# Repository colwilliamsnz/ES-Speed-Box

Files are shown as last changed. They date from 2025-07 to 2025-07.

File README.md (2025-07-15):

# ES-Speed-Box for controlling Pro-Ject Turntables with 16VAC Synchronous Motors.

## Status:

Prototype.

## Introduction:

A speed controller to suit Pro-Ject Turntables with 16VAC synchronous motors (Expression 3, etc). A clone of sorts of the off the shelf line of Pro-ject "SpeedBox" devices that allows for 33RPM and 45RPM speed selection electronically instead of changing the belt/pulley beneath the turntable platter.

Speed selection is controlled in software using a DDS (direct digital synthesis) IC to generate a sinusoidal waveform of the appropriate frequency (~50Hz for 33RPM, ~67 for 45RPM). An I2C header allows for an optional external OLED screen to display speed selection. An 18VDC output provides power to a Pro-Ject Phonobox. The device can be WiFi enabled to allow the speed to be controlled remotely using MQTT auto-discovery via HomeAssistant.

Power to the circuit is controlled via an SSR (solid state relay) and is intended to be connected to a 12V amplifier trigger output. Thus the device has no phantom power draw and only powers the turntable when the amplifier trigger output is on.

## Project Goals:

1. Powered on when the amplifier is on/phono aux input is on.
2. Provide power to both the turntable but also an Phono Box II pre-amp.
3. I2C interface to allow connection of an OLED screen to display speed and amp volume (amp volume via Yamaha API).
4. Low profile design to fit in a small rack mountable case.

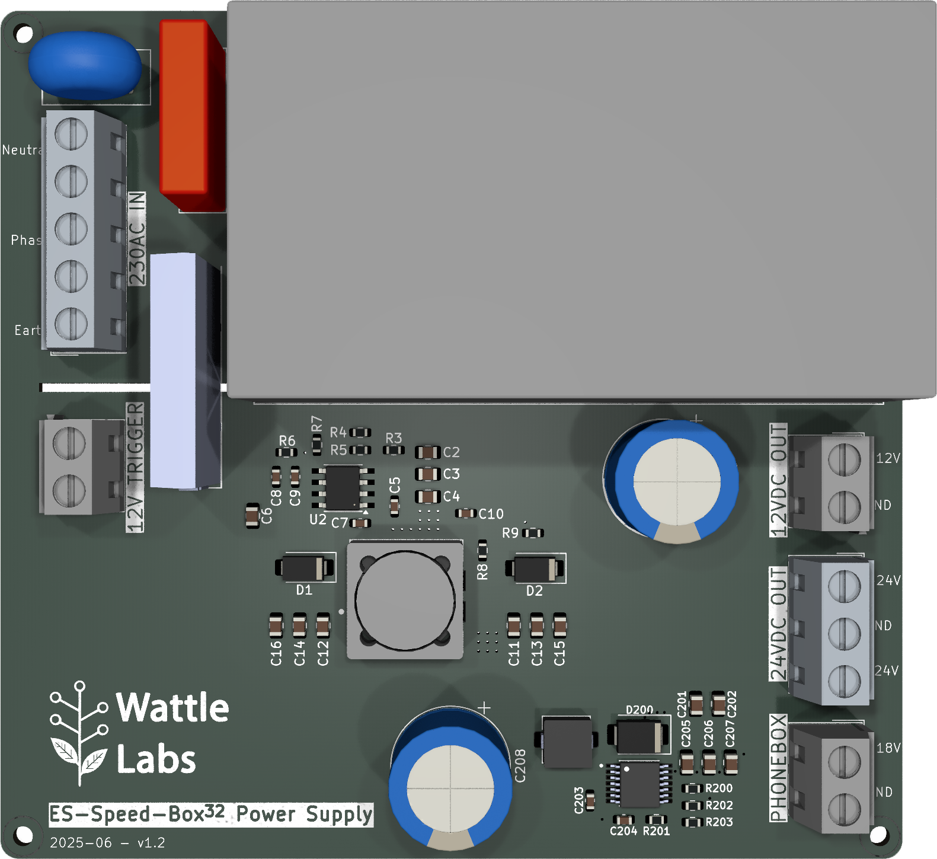
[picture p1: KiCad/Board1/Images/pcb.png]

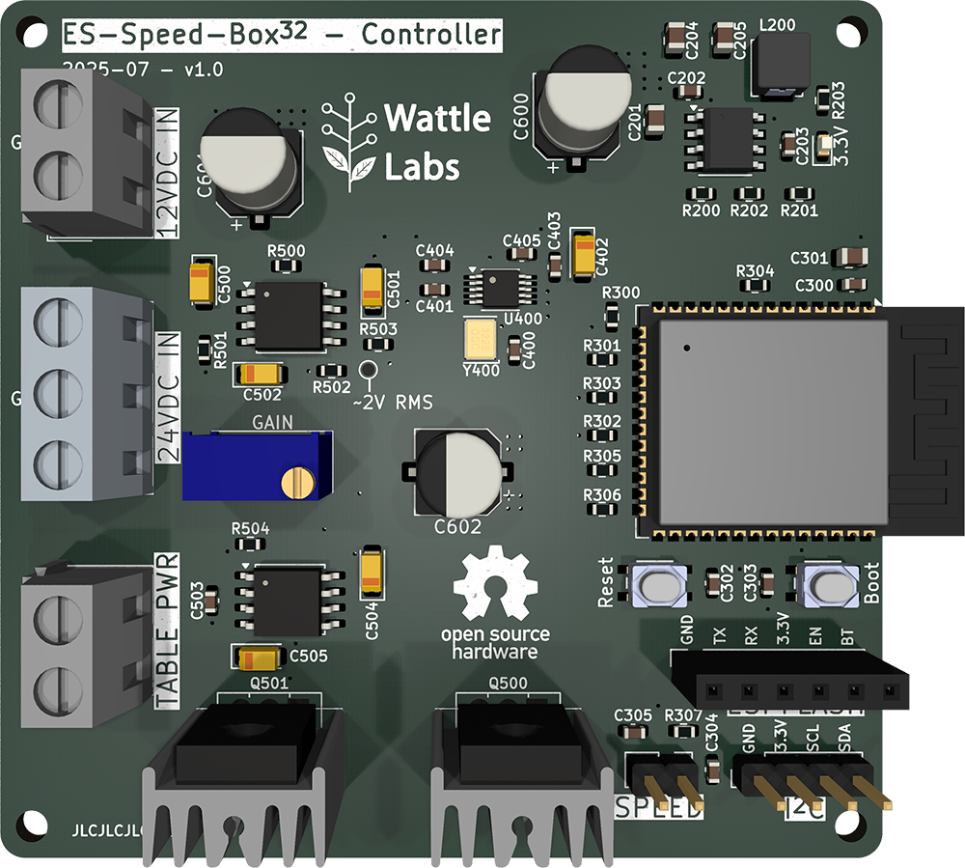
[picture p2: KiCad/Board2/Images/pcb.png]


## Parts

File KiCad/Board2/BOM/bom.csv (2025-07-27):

Reference | Value | Footprint | Qty | Digikey_PN
C402,C500 | 10u | Capacitor_Tantalum_SMD:CP_EIA-3216-18_Kemet-A | 2 | 399-8269-1-ND
C501,C502,C504,C505 | 1u | Capacitor_Tantalum_SMD:CP_EIA-3216-18_Kemet-A | 4 | 478-1651-1-ND
C600,C601,C602 | 47u | Capacitor_SMD:CP_Elec_6.3x7.7 | 3 | 493-2225-1-ND
L200 | 4.7uH | Wattle_Inductors:Bournes_SRP4020TA-4R7M | 1 | SRP4020TA-4R7MCT-ND
Q500 | BD139 | Package_TO_SOT_THT:TO-126-3_Vertical | 1 | 497-6656-5-ND
Q501 | BD140 | Package_TO_SOT_THT:TO-126-3_Vertical | 1 | 497-6657-5-ND
RV500 | 10k | Wattle_Trimpots:PV36W103C01B00 | 1 | 118-PV36W103C01B00-ND
SW300 | Reset | Wattle_Switches:PTS810 | 2 | CKN10878CT-ND
U200 | AP64352Q | Wattle_Regulators:AP64352QSP-13 | 1 | 31-AP64352QSP-13CT-ND
U300 | ESP32-S3-WROOM-1 | RF_Module:ESP32-S3-WROOM-1 | 1 | 1965-ESP32-S3-WROOM-1U-N8CT-ND
U400 | AD9833BRMZ | Package_SO:MSOP-10_3x3mm_P0.5mm | 1 | AD9833BRMZ
U500,U501 | OPA604AU/2K5 | Package_SO:SOIC-8_5.3x5.3mm_P1.27mm | 2 | 296-46167-1-ND
Y400 | 24Mhz | Oscillator:Oscillator_SMD_EuroQuartz_XO32-4Pin_3.2x2.5mm | 1 | 1908-O240-JO32-B-1V3-1-T1-LFCT-ND

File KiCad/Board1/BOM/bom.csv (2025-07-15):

Reference | Value | Footprint | Qty | Digikey_PN
C1 | 10n | Capacitor_THT:C_Rect_L18.0mm_W5.0mm_P15.00mm_FKS3_FKP3 | 1 | BFC233841103-ND
C2,C3,C4,C6,C11,C12,C13,C14,C15,C16 | 22u | Capacitor_SMD:C_0805_2012Metric | 10 | 445-14428-1-ND
C5,C7,C8 | 100n | Capacitor_SMD:C_0603_1608Metric | 3 | 587-3354-1-ND
C9 | 330p | Capacitor_SMD:C_0603_1608Metric | 1 | 399-C0603C331K5RACTUCT-ND
C10 | 470p | Capacitor_SMD:C_0603_1608Metric | 1 | 399-C0603C471F5GACTUCT-ND
C200,C208 | 1000u | Capacitor_THT:CP_Radial_D13.0mm_P5.00mm | 2
C201,C202 | 10u | Capacitor_SMD:C_0805_2012Metric | 2 | 490-10515-1-ND
C203 | 47n | Capacitor_SMD:C_0603_1608Metric | 1 | 490-5854-1-ND
C204 | 15n | Capacitor_SMD:C_0603_1608Metric | 1 | 311-1430-1-ND
C205,C206,C207 | 4.7 | Capacitor_SMD:C_0805_2012Metric | 3 | 490-10751-1-ND
D1,D2 | B360A | Diode_SMD:D_SMA | 2 | B360A-M3/61TGICT-ND
D200 | B360B-13-F | Diode_SMD:D_SMB | 1 | B360B-FDICT-ND
L1 | 2x33uH | Wattle_Inductors:Bournes_SRF1260-330M | 1 | SRF1260-330MCT-ND
L200 | 10uH | Wattle_Inductors:Bournes_SRP5030T-100M | 1 | SRP5030T-100MCT-ND
R1,R2 | 2M | Resistor_SMD:R_2010_5025Metric_Pad1.40x2.65mm_HandSolder | 2 | 2019-HV732HTTE2004FCT-ND
R3 | 280k | Resistor_SMD:R_0603_1608Metric | 1 | 311-280KHRCT-ND
R4 | 49.9k | Resistor_SMD:R_0603_1608Metric | 1 | 541-3989-1-ND
R5 | 412k | Resistor_SMD:R_0603_1608Metric | 1 | 311-412KHRCT-ND
R6 | 10k | Resistor_SMD:R_0603_1608Metric | 1 | A121523CT-ND
R7 | 2k | Resistor_SMD:R_0603_1608Metric | 1 | 541-3953-1-ND
R8 | 100 | Resistor_SMD:R_0603_1608Metric | 1 | 311-100HRCT-ND
R9 | 118k | Resistor_SMD:R_0603_1608Metric | 1 | 541-118KHCT-ND
R200 | 105k | Resistor_SMD:R_0603_1608Metric | 1 | 13-AC0603FR-07105KLCT-ND
R201 | 3.83k | Resistor_SMD:R_0603_1608Metric | 1 | 311-3.83KHRCT-ND
R202 | 221k | Resistor_SMD:R_0603_1608Metric | 1 | 311-221KHRCT-ND
R203 | 16.2k | Resistor_SMD:R_0603_1608Metric | 1 | 311-16.2KHRCT-ND
RV1 | 10D561 | Varistor:RV_Disc_D12mm_W6.1mm_P7.5mm | 1 | 118-MOV-10D561K-ND
S1 | AQG22212 | Wattle_Relays:AQG22212 | 1 | 255-3751-ND
U1 | IRM-30-12 | Wattle_Power:IRM-30-12 | 1 | 1866-3043-ND
U2 | TPS54340DDA | Package_SO:TI_SO-PowerPAD-8_ThermalVias | 1 | 296-35495-5-ND
U200 | TPS61175PWPR | Wattle_Regulators:TPS61175 | 1 | 296-24013-1-ND

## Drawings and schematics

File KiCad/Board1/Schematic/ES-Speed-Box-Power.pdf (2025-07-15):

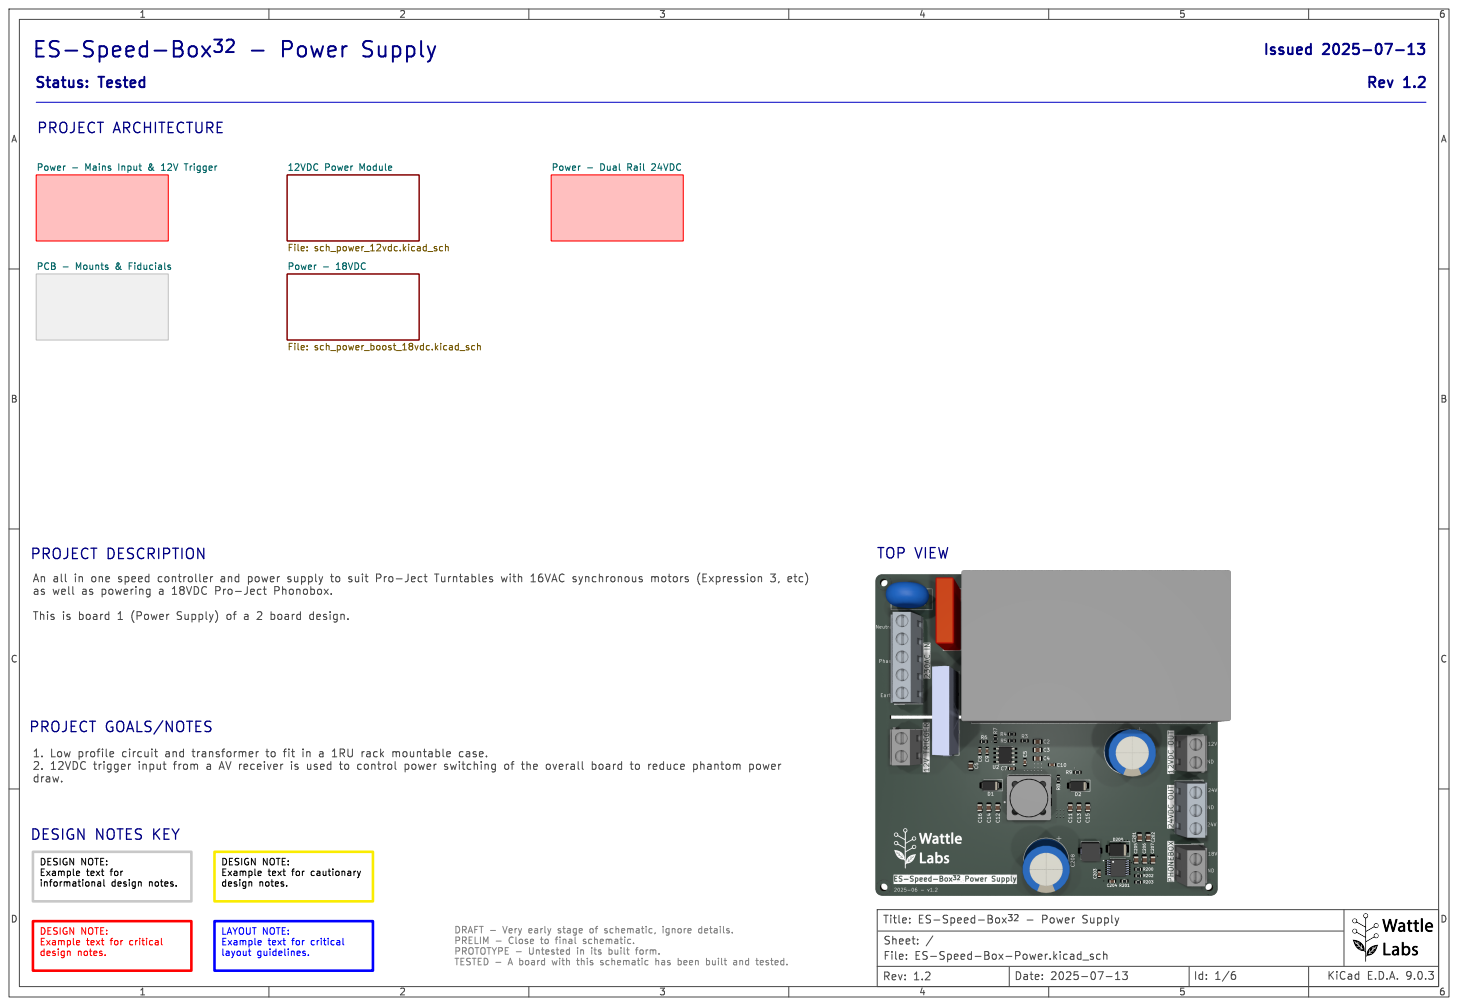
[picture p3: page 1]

DESIGN NOTE: Example text for critical design notes. DESIGN NOTE: Example text for

design notes. LAYOUT NOTE: Example text for critical

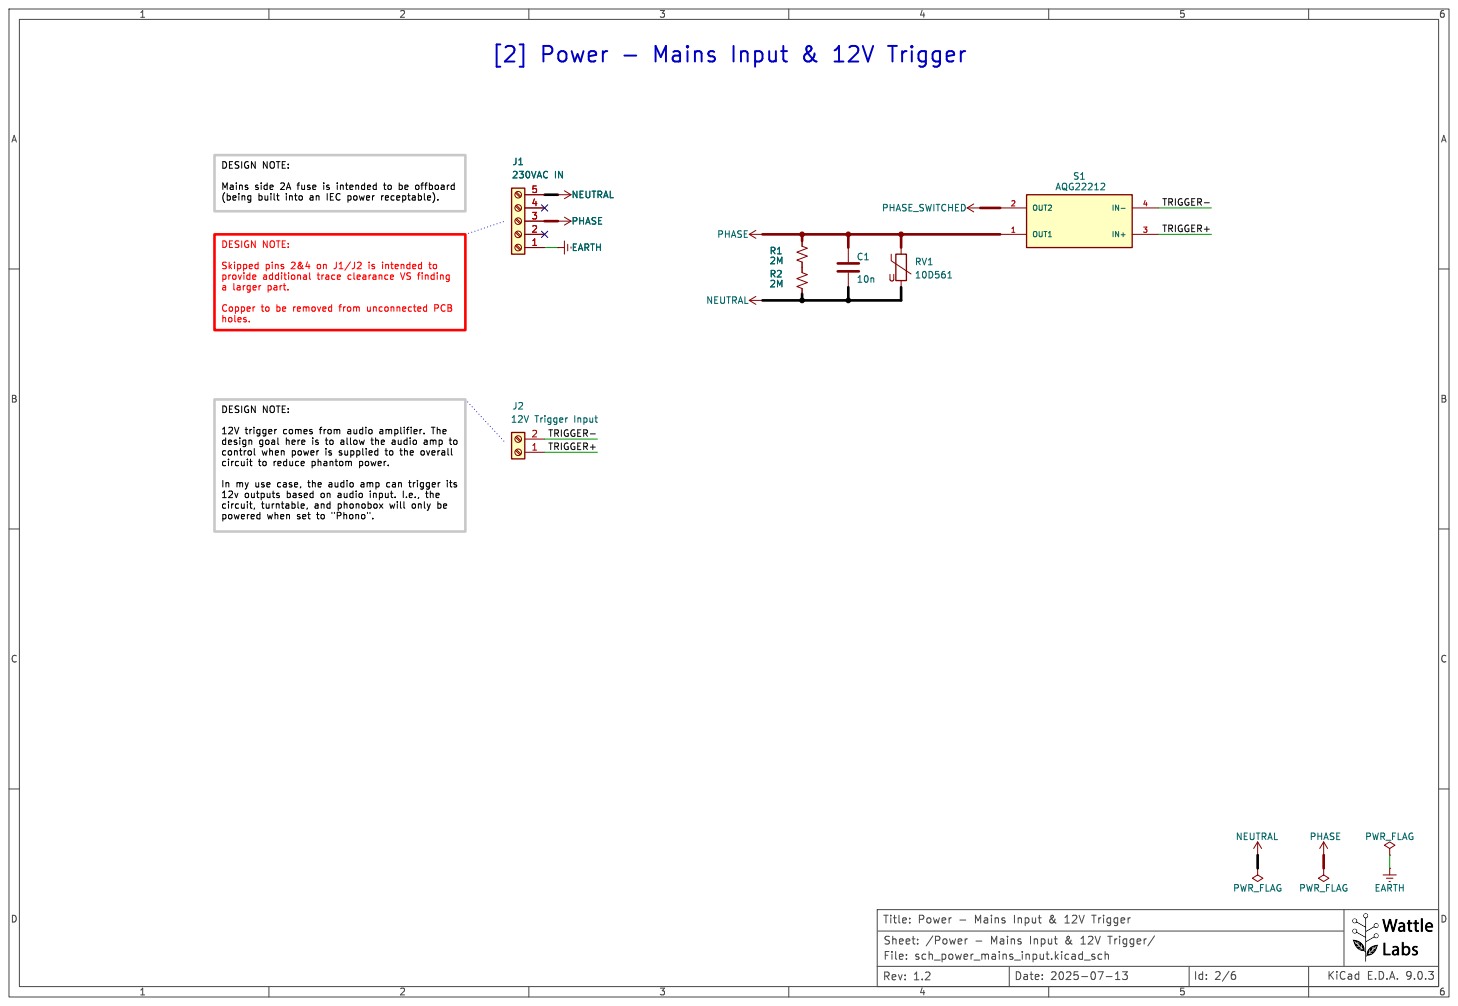
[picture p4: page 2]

design goal here is to allow the audio amp to

In my use case, the audio amp can trigger its 12v outputs based on audio input. I.e., the

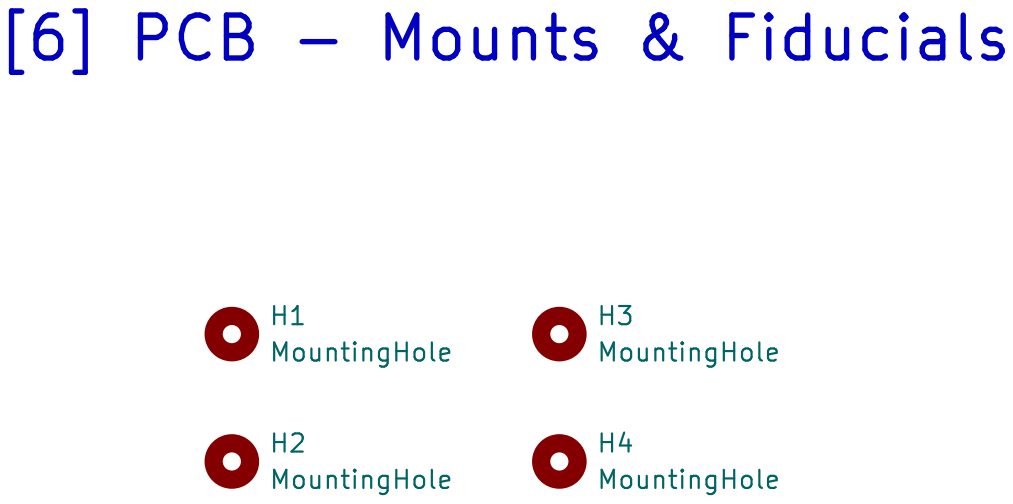
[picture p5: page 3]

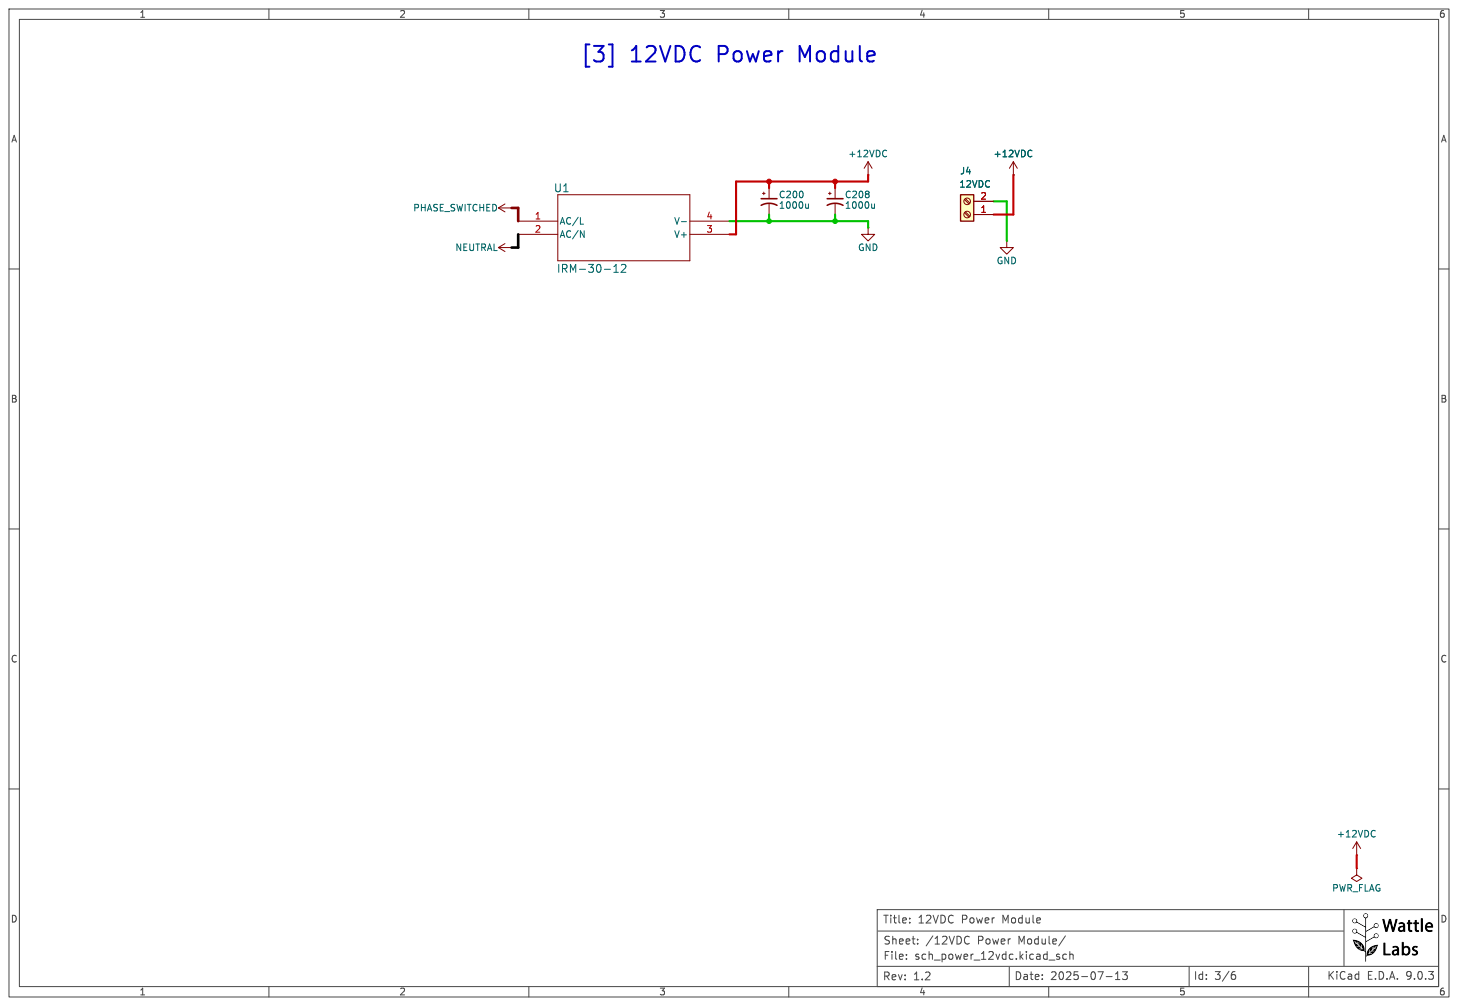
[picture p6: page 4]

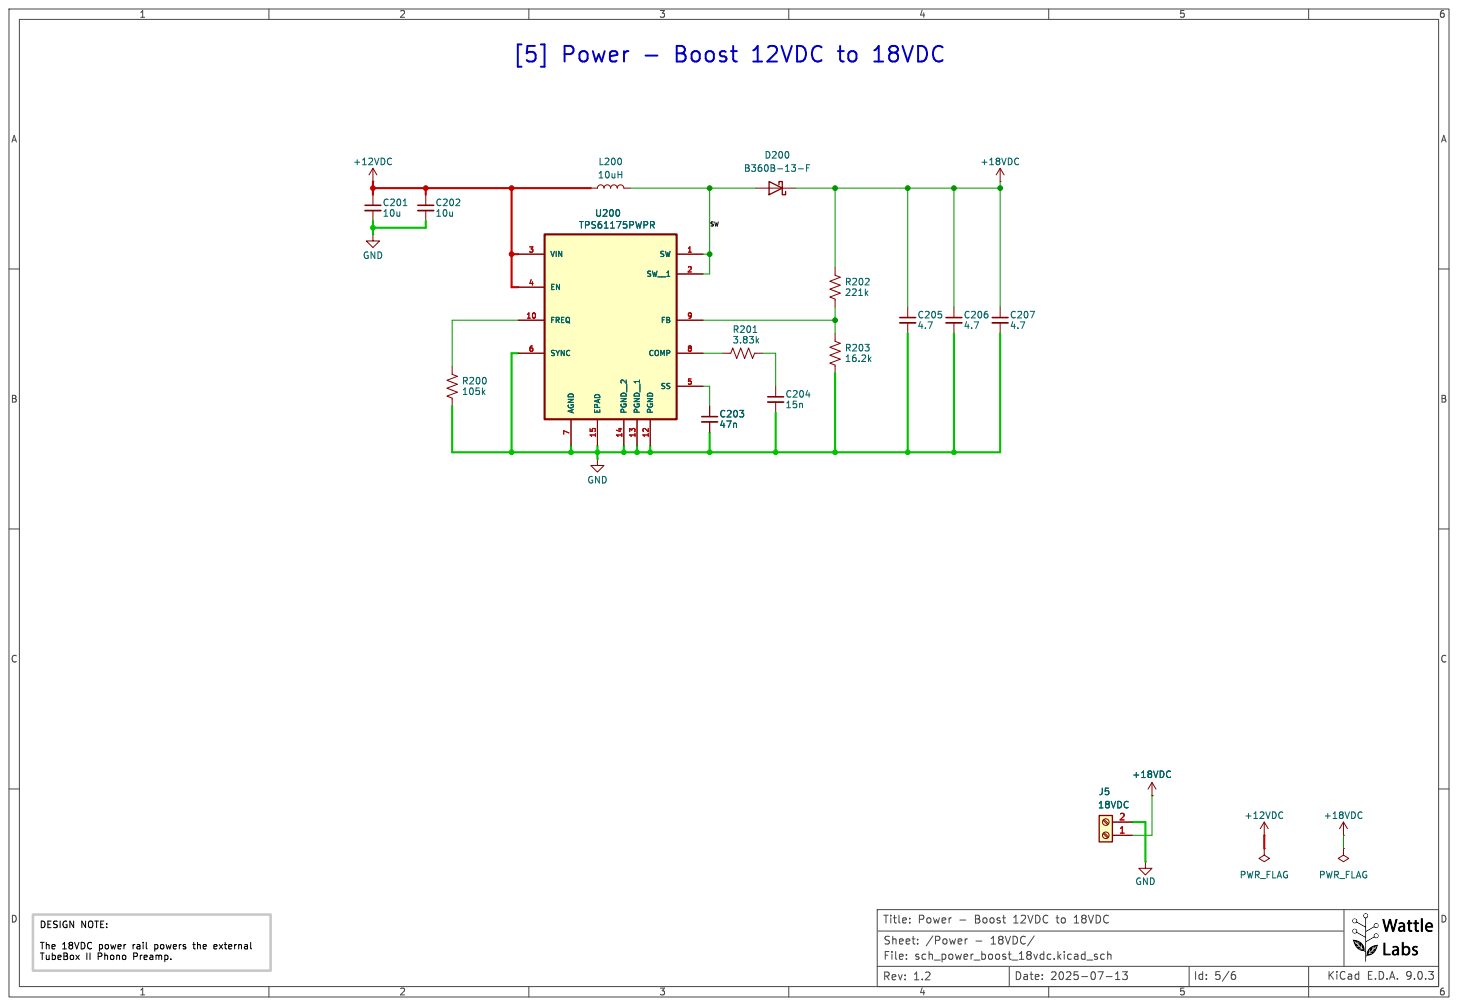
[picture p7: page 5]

7 EPAD 15 PGND__2 14 PGND__1 13 PGND 12 SW 1 SW__1 2 FB 9 COMP 8 SS 5 U200 TPS61175PWPR

7 EPAD 15 PGND__2 14 PGND__1 13 PGND 12 SW 1 SW__1 2 FB 9 COMP 8 SS 5 C203

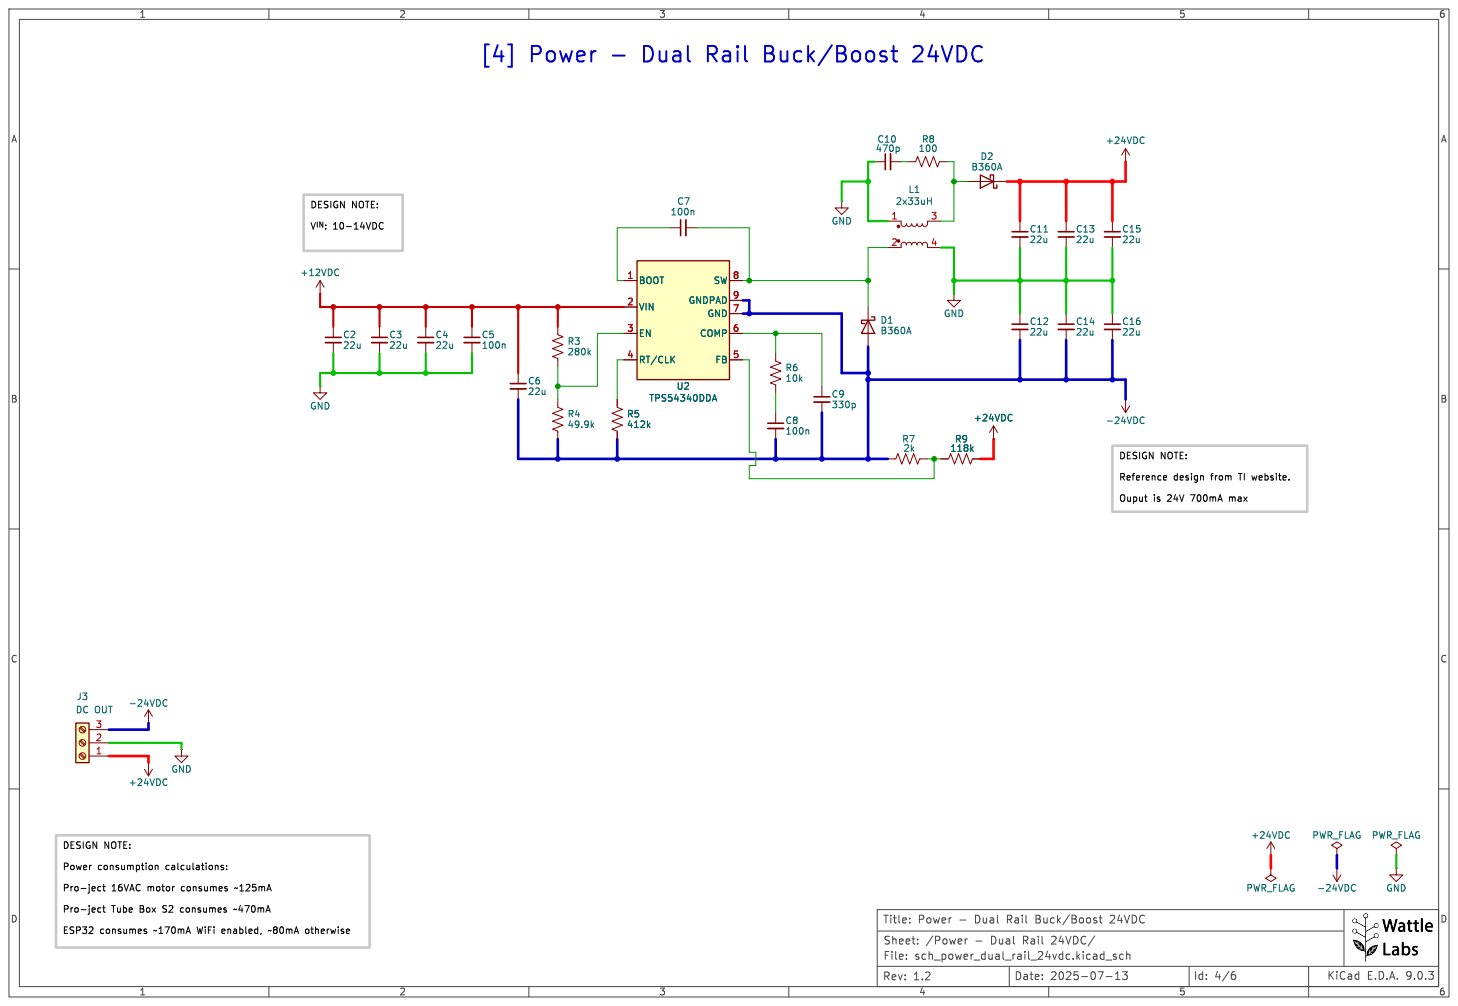
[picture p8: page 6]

DESIGN NOTE: Reference design from TI website. Ouput is 24V 700mA max R9

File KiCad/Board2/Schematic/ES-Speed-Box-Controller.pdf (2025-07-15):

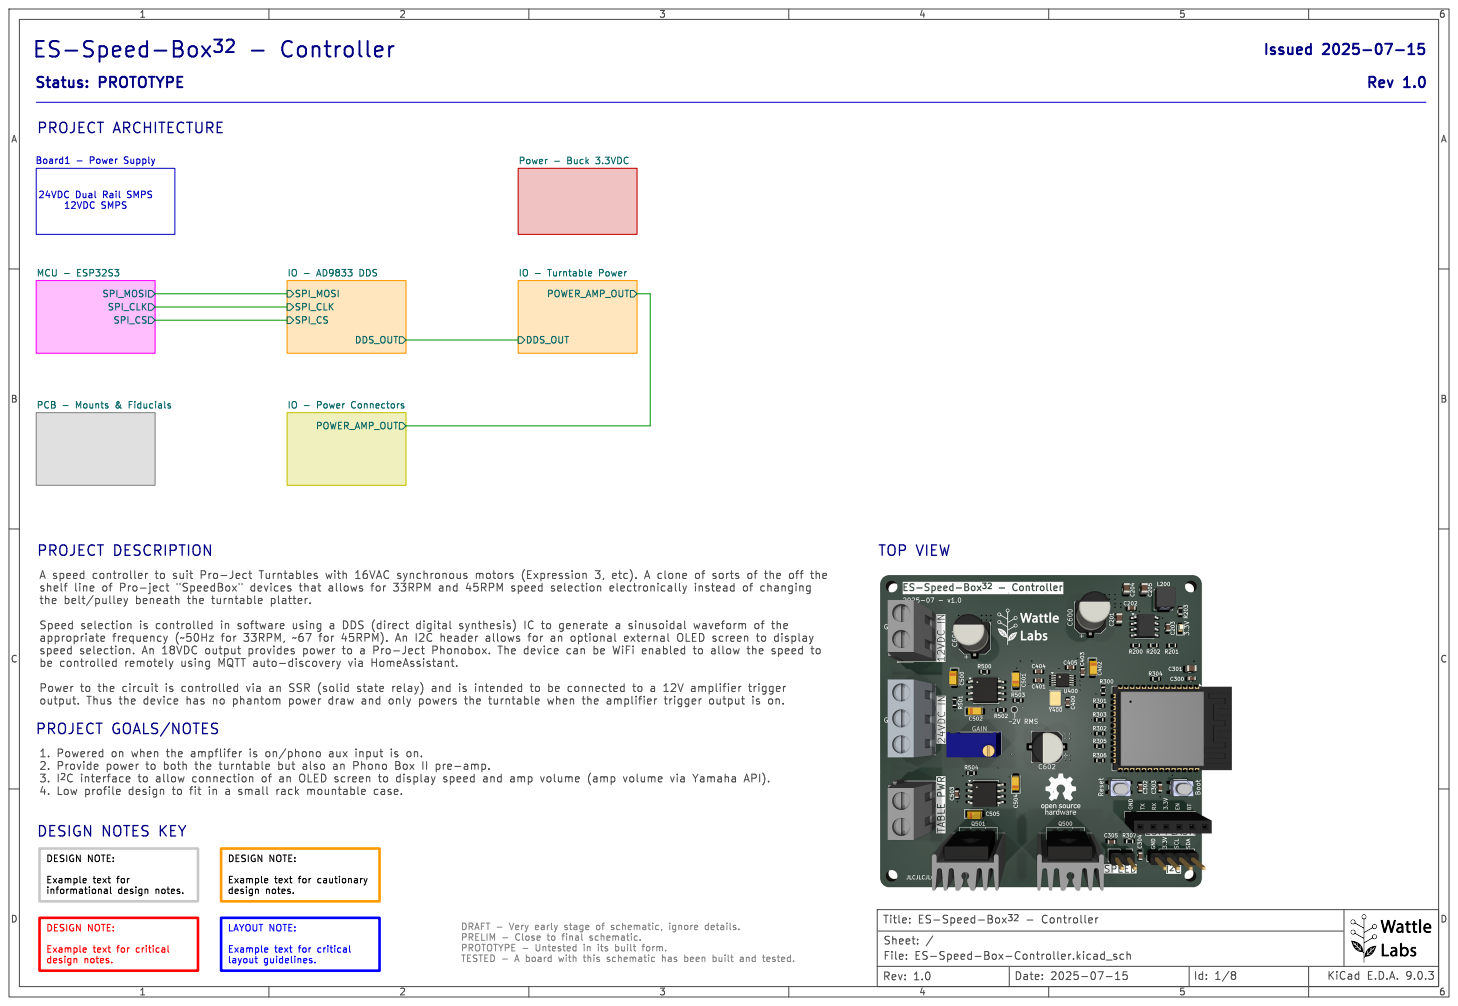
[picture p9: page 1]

design notes. DESIGN NOTE: Example text for

layout guidelines. DESIGN NOTE: Example text for cautionary

LAYOUT NOTE: Example text for critical

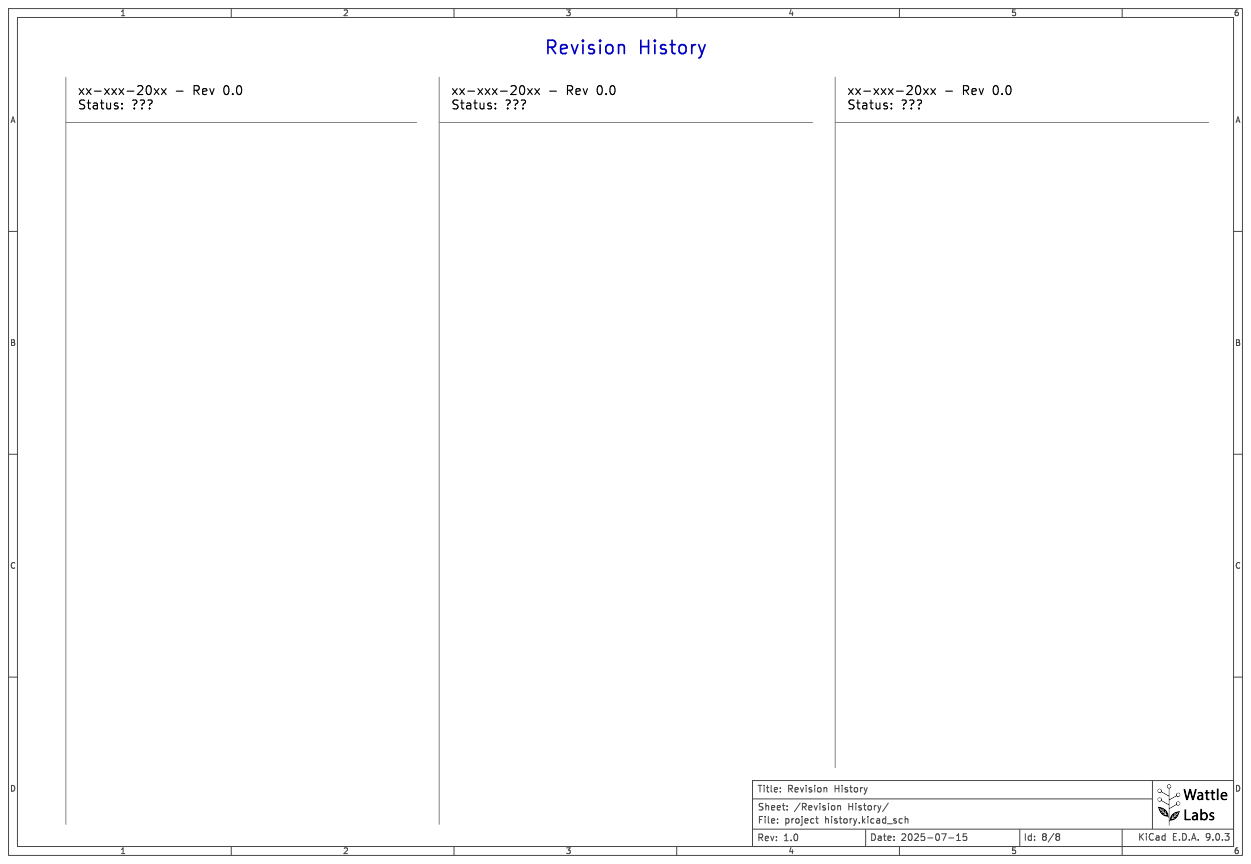
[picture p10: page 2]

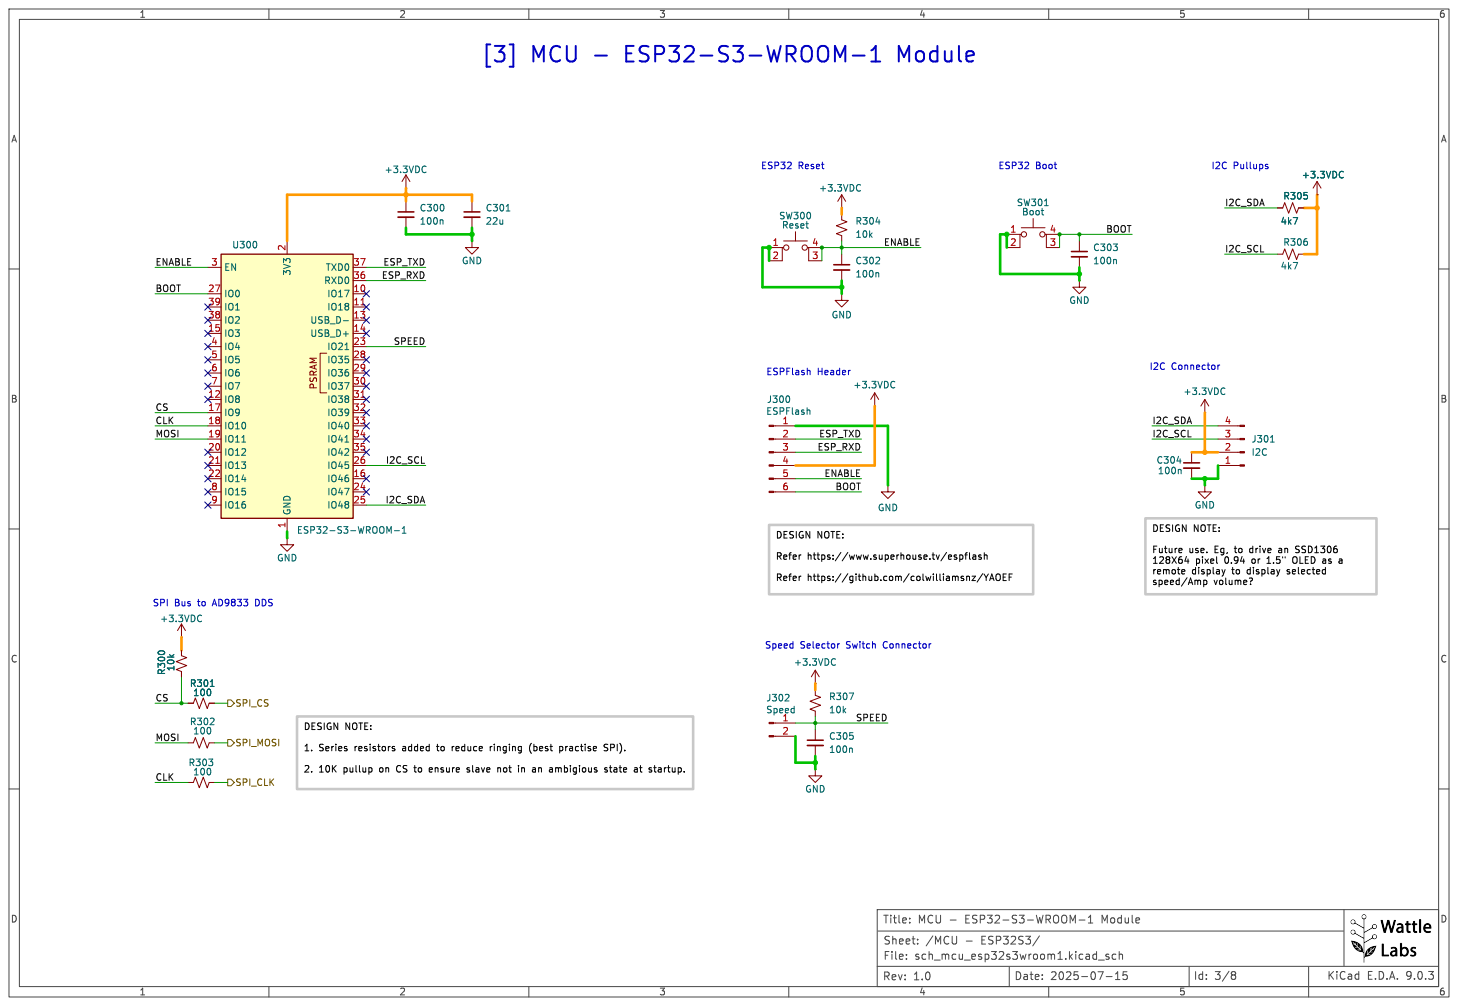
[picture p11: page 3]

128X64 pixel 0.94 or 1.5" OLED as a
remote display to display selected

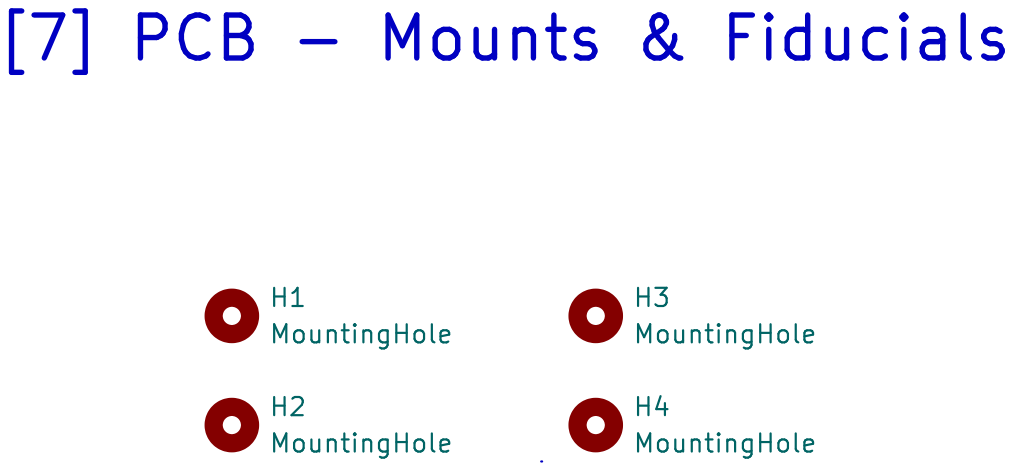
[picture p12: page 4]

H3 MountingHole H4 MountingHole H2 MountingHole H1 MountingHole

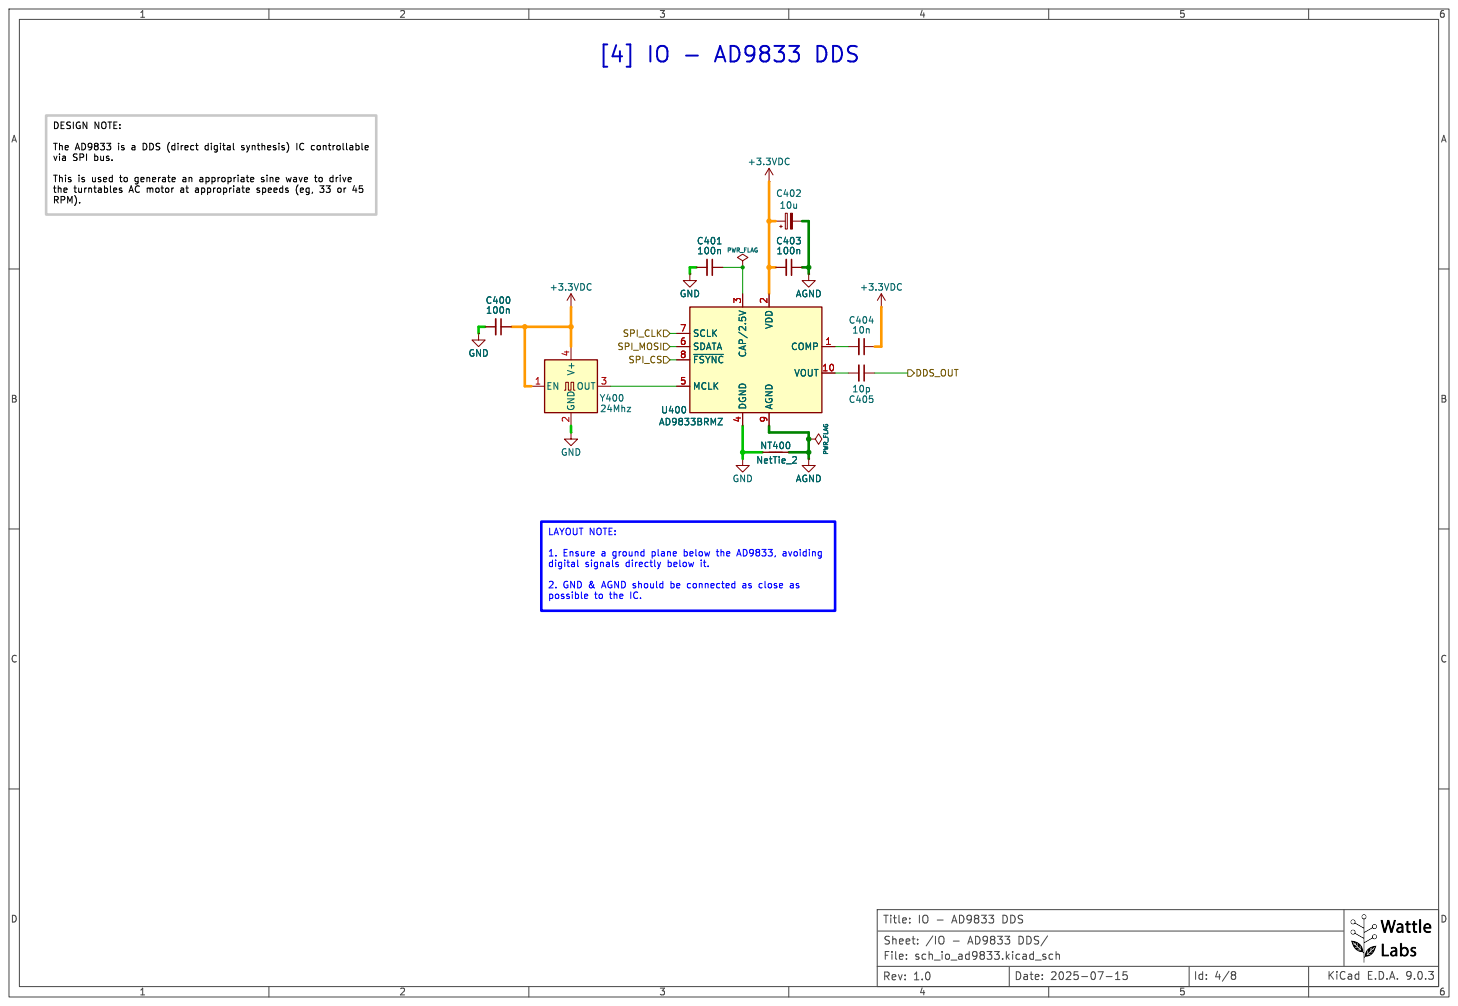
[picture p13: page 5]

SPI_MOSI LAYOUT NOTE: 1. Ensure a ground plane below the AD9833, avoiding

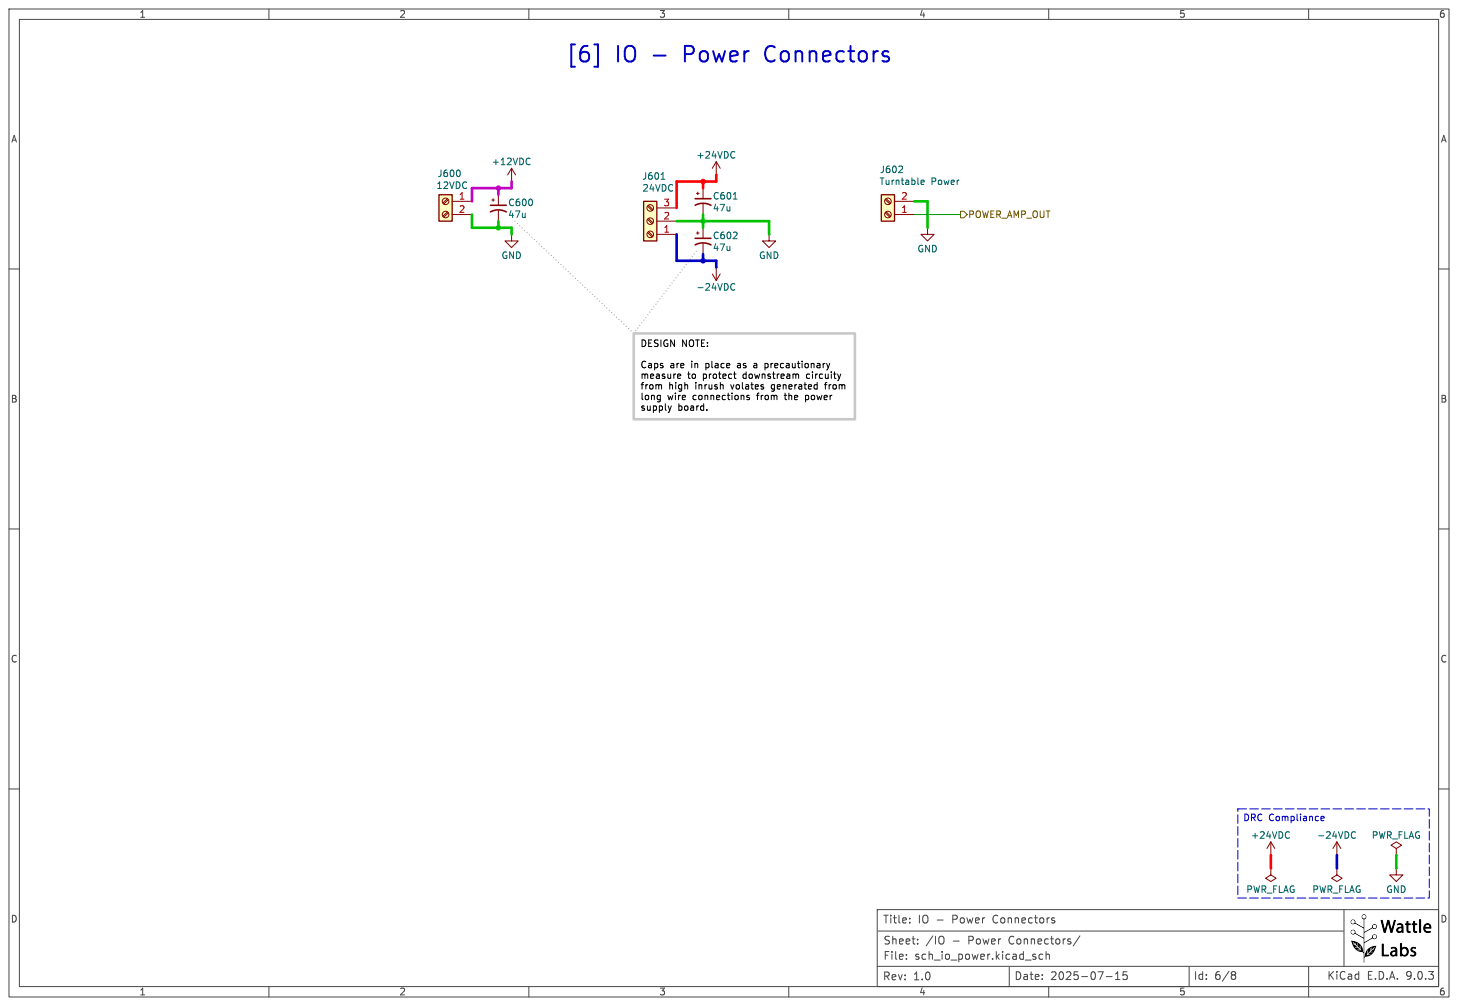
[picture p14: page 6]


7 BST 1 SW 8 FB 5 SS 6 U200 AP64352Q C201

7 BST 1 SW 8 FB 5 SS 6

output DESIGN NOTE: The 3.3VDC power rail powers the MCU and AD9833. DESIGN NOTE: V_{IN}:3.8V-40V


1 NC 8 OUT 6 GND R500 1k GND
1u U500 OPA604AU/2K5

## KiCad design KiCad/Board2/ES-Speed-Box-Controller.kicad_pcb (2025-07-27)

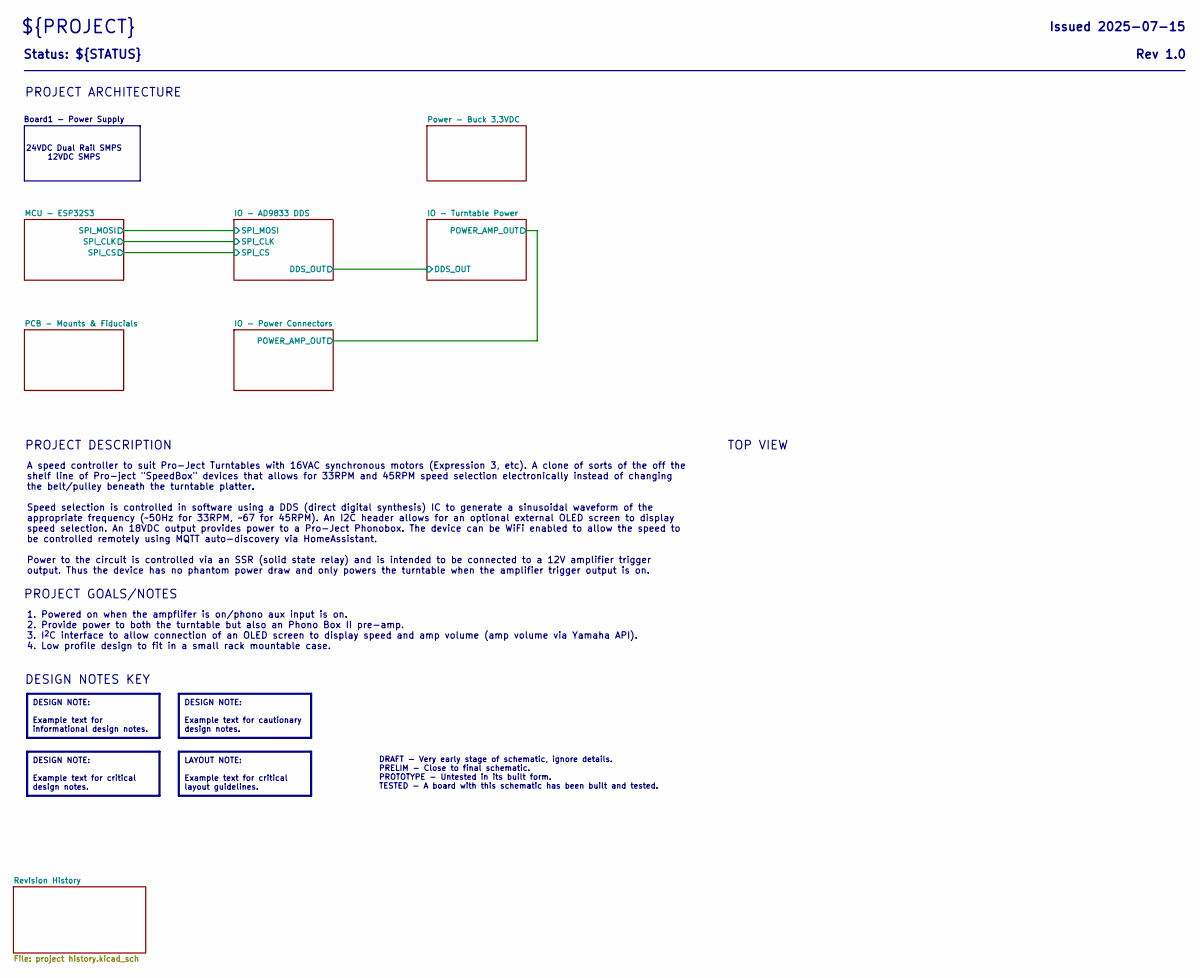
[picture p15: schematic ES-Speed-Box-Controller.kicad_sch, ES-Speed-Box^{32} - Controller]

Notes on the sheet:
PROJECT DESCRIPTION
PROJECT GOALS/NOTES
TOP VIEW
Board1 - Power Supply
DESIGN NOTES KEY
PROJECT ARCHITECTURE
24VDC Dual Rail SMPS 12VDC SMPS
DESIGN NOTE: Example text for critical design notes.
DESIGN NOTE: Example text for informational design notes.
DESIGN NOTE: Example text for cautionary design notes.
Status: ${STATUS}
DRAFT - Very early stage of schematic, ignore details. PRELIM - Close to final schematic. PROTOTYPE - Untested in its built form. TESTED - A board with this schematic has been built and tested.
1. Powered on when the ampflifer is on/phono aux input is on. 2. Provide power to both the turntable but also an Phono Box II pre-amp. 3. I^{2}C interface to allow connection of an OLED screen to display speed and amp volume (amp volume via Yamaha API). 4. Low profile design to fit in a small rack 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
Rev ${REVISION}
A speed controller to suit Pro-Ject Turntables with 16VAC synchronous motors (Expression 3, etc). A clone of sorts of the off the shelf line of Pro-ject "SpeedBox" devices that allows for 33RPM and 45RPM speed selection electronically instead of changing the belt/pulley beneath the turntable platte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
${PROJECT}
LAYOUT NOTE: Example text for critical layout guidelines.
Issued ${ISSUE_DATE}

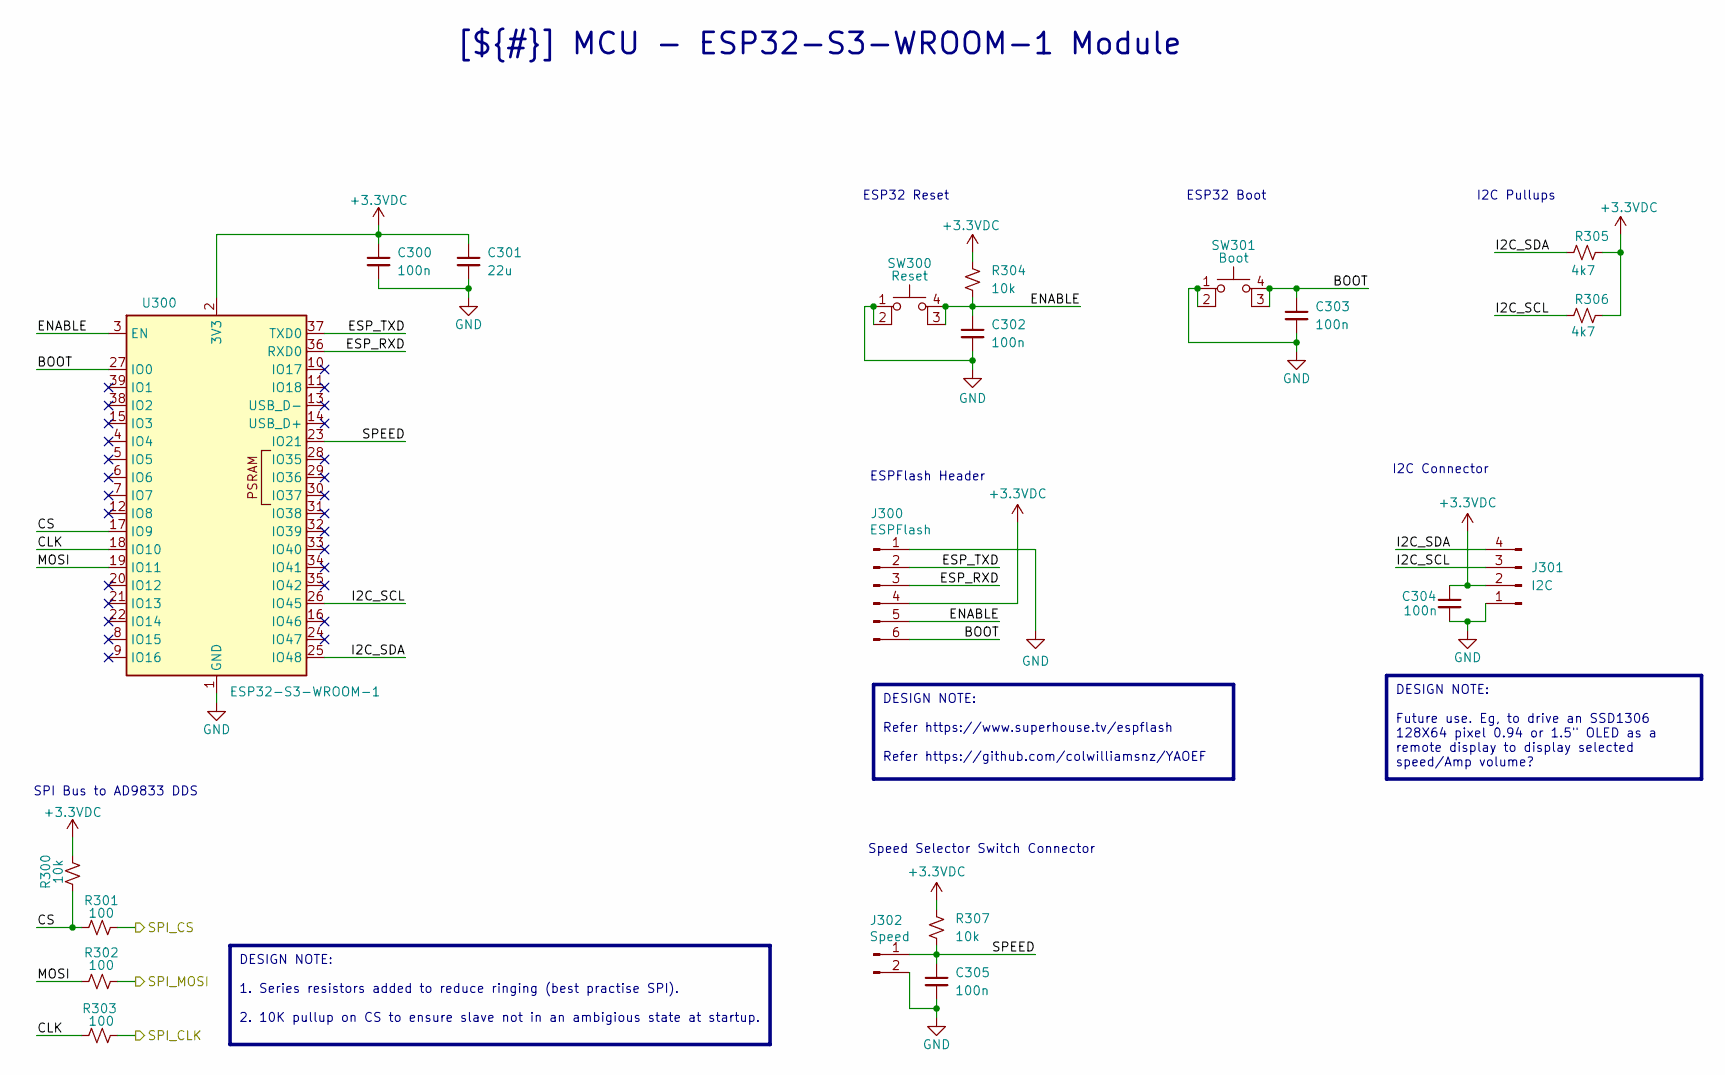
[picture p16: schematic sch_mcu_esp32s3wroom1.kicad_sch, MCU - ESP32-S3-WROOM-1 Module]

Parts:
C300, C302, C303, C304, C305: 100n; C_0603_1608Metric; Digikey_PN 399-C0603C104K4RACTUCT-ND
C301: 22u; C_0805_2012Metric; Digikey_PN 445-14428-1-ND
J300: ESPFlash; PinSocket_1x06_P2.54mm_Vertical; Digikey_PN 61300611821
J301: I2C; PinHeader_1x04_P2.54mm_Vertical
J302: Speed; PinHeader_1x02_P2.54mm_Vertical
R300, R304, R307: 10k; R_0603_1608Metric; Digikey_PN 541-10.0KHCT-ND
R301, R302, R303: 100; R_0603_1608Metric; Digikey_PN 311-100HRCT-ND
R305, R306: 4k7; R_0603_1608Metric; Digikey_PN 541-3993-1-ND
SW300: Reset; PTS810; Digikey_PN CKN10878CT-ND
SW301: Boot; PTS810; Digikey_PN CKN10878CT-ND
U300: ESP32-S3-WROOM-1; Digikey_PN 1965-ESP32-S3-WROOM-1U-N8CT-ND

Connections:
+3.3VDC: C300.1, C301.1, C304.1, J300.4, J301.2, R300.2, R304.2, R305.1, R306.1, R307.2, U300.2 (3V3); also elsewhere on the board
/IO - AD9833 DDS/SPI_CLK: R303.2; also elsewhere on the board
/IO - AD9833 DDS/SPI_CS: R301.2; also elsewhere on the board
/IO - AD9833 DDS/SPI_MOSI: R302.2; also elsewhere on the board
/MCU - ESP32S3/BOOT: C303.1, J300.6, SW301.3 (K), SW301.4 (A), U300.27 (IO0)
/MCU - ESP32S3/CLK: R303.1, U300.18 (IO10)
/MCU - ESP32S3/CS: R300.1, R301.1, U300.17 (IO9)
/MCU - ESP32S3/ENABLE: C302.1, J300.5, R304.1, SW300.3 (K), SW300.4 (A), U300.3 (EN)
/MCU - ESP32S3/ESP_RXD: J300.3, U300.36 (RXD0)
/MCU - ESP32S3/ESP_TXD: J300.2, U300.37 (TXD0)
/MCU - ESP32S3/I2C_SCL: J301.3, R306.2, U300.26 (IO45)
/MCU - ESP32S3/I2C_SDA: J301.4, R305.2, U300.25 (IO48)
/MCU - ESP32S3/MOSI: R302.1, U300.19 (IO11)
/MCU - ESP32S3/SPEED: C305.1, J302.1, R307.1, U300.23 (IO21)
GND: C300.2, C301.2, C302.2, C303.2, C304.2, C305.2, J300.1, J301.1, J302.2, SW300.1, SW300.2, SW301.1, SW301.2, U300.1 (GND), U300.40 (GND), U300.41 (GND); also elsewhere on the board

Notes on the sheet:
I2C Connector
I2C Pullups
Speed Selector Switch Connector
ESP32 Reset
ESP32 Boot
ESPFlash Header
SPI Bus to AD9833 DDS
DESIGN NOTE: 1. Series resistors added to reduce ringing (best practise SPI). 2. 10K pullup on CS to ensure slave not in an ambigious state at startup.
DESIGN NOTE: Future use. Eg, to drive an SSD1306 128X64 pixel 0.94 or 1.5" OLED as a remote display to display selected speed/Amp volume?
[${#}] ${TITLE}
DESIGN NOTE: Refer https://www.superhouse.tv/espflash Refer https://github.com/colwilliamsnz/YAOEF

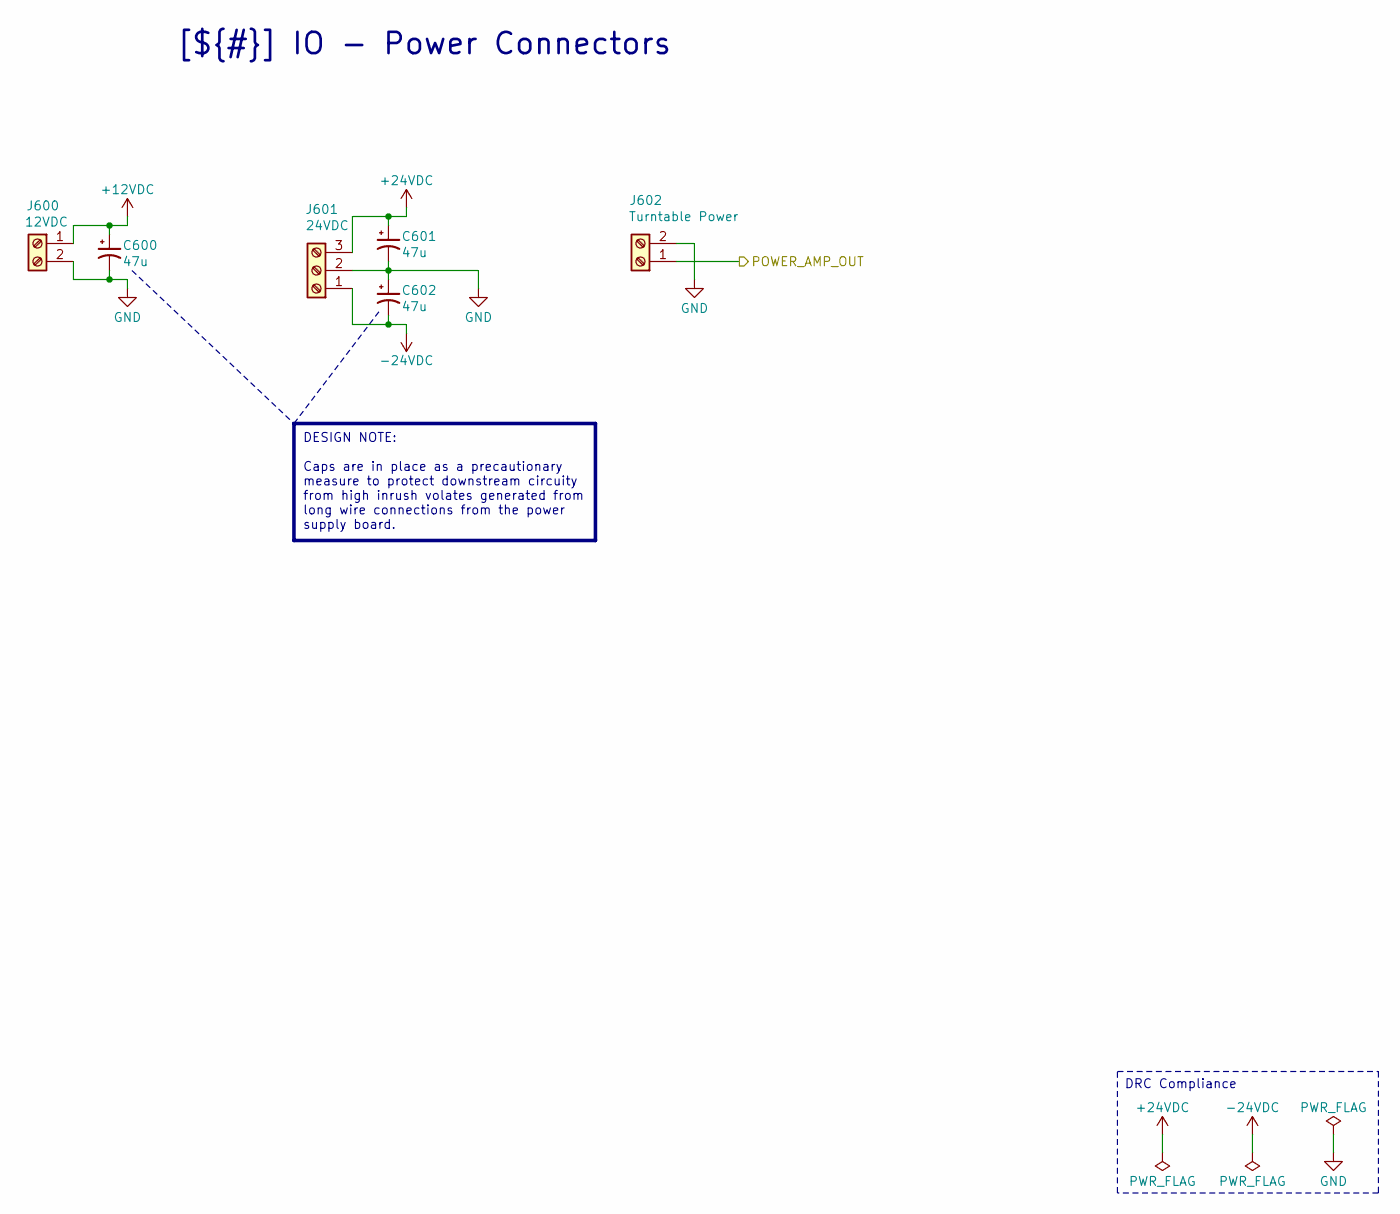
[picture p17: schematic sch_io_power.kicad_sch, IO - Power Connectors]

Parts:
C600, C601, C602: 47u; CP_Elec_6.3x7.7; Digikey_PN 493-2225-1-ND
J600: 12VDC; TerminalBlock_1x02_P5.00mm
J601: 24VDC; TerminalBlock_1x03_P5.00mm
J602: Turntable Power; TerminalBlock_1x02_P5.00mm

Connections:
+12VDC: C600.1, J600.1; also elsewhere on the board
+24VDC: C601.1, J601.3; also elsewhere on the board
-24VDC: C602.2, J601.1; also elsewhere on the board
/IO - Power Connectors/POWER_AMP_OUT: J602.1; also elsewhere on the board
GND: C600.2, C601.2, C602.1, J600.2, J601.2, J602.2; also elsewhere on the board

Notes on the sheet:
DESIGN NOTE: Caps are in place as a precautionary measure to protect downstream circuity from high inrush volates generated from long wire connections from the power supply board.
DRC Compliance
[${#}] ${TITLE}

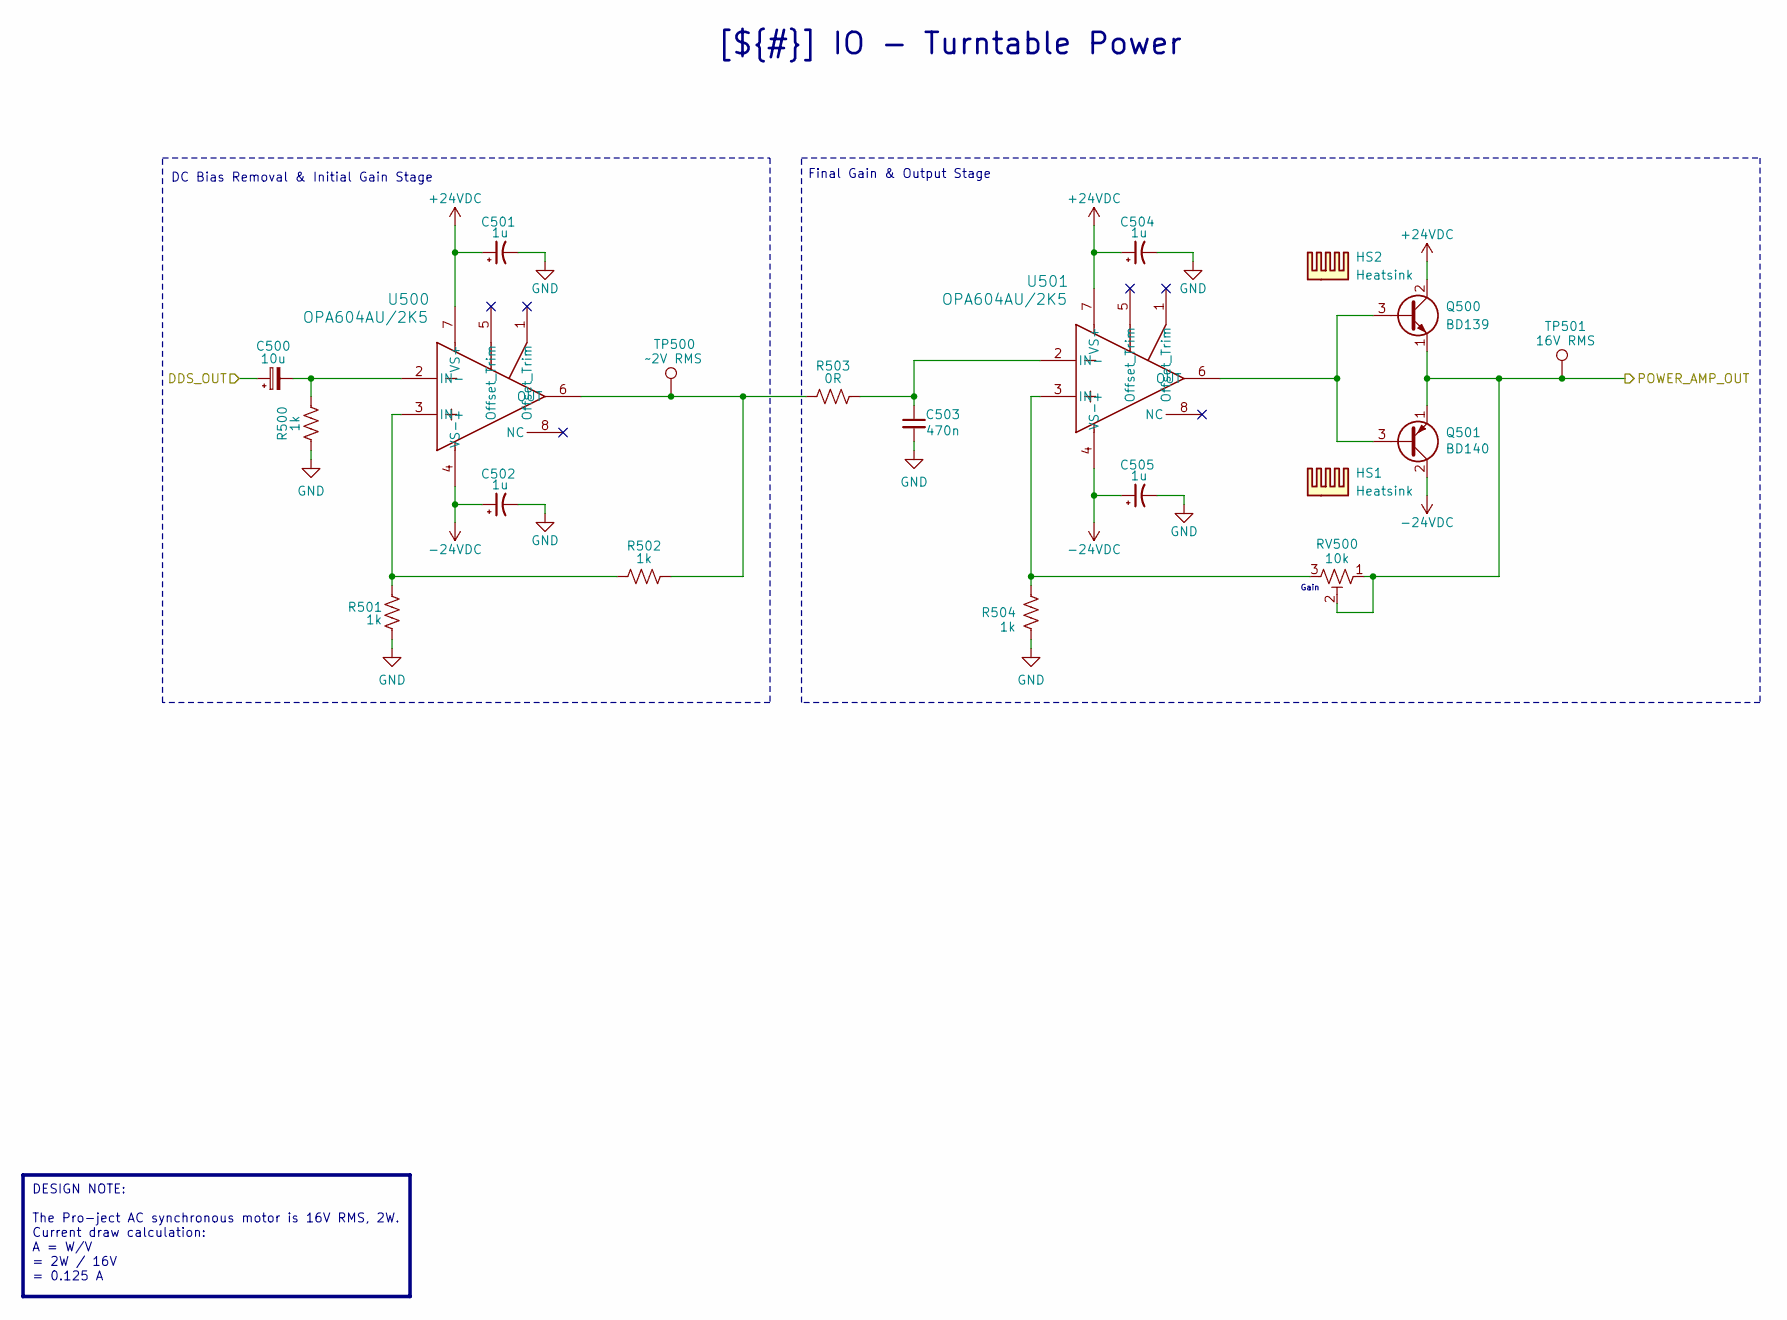
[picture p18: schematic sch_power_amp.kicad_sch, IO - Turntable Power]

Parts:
C500: 10u; CP_EIA-3216-18_Kemet-A; Digikey_PN 399-8269-1-ND
C501, C502, C504, C505: 1u; CP_EIA-3216-18_Kemet-A; Digikey_PN 478-1651-1-ND
C503: 470n; C_0603_1608Metric; Digikey_PN 1276-CL10B474KO8VPJCCT-ND
HS1, HS2: Heatsink; V5629; Digikey_PN AE10825-ND
Q500: BD139; TO-126-3_Vertical; Digikey_PN 497-6656-5-ND
Q501: BD140; TO-126-3_Vertical; Digikey_PN 497-6657-5-ND
R500, R501, R502, R504: 1k; R_0603_1608Metric; Digikey_PN MCT0603-1.00K-MFCT-ND
R503: 0R; R_0603_1608Metric; Digikey_PN 4988-NRC06ZOTRFCT-ND
RV500: 10k; PV36W103C01B00; Digikey_PN 118-PV36W103C01B00-ND
TP500: ~2V RMS; TestPoint_Pad_D1.0mm
TP501: 16V RMS; TestPoint_Pad_D1.0mm
U500, U501: OPA604AU/2K5; SOIC-8_5.3x5.3mm_P1.27mm; Digikey_PN 296-46167-1-ND

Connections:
+24VDC: C501.1, C504.1, Q500.2 (C), U500.7 (VS+), U501.7 (VS+); also elsewhere on the board
-24VDC: C502.1, C505.1, Q501.2 (C), U500.4 (VS-), U501.4 (VS-); also elsewhere on the board
/IO - AD9833 DDS/DDS_OUT: C500.1; also elsewhere on the board
/IO - Power Connectors/POWER_AMP_OUT: Q500.1 (E), Q501.1 (E), RV500.1, RV500.2, TP501.1; also elsewhere on the board
GND: C501.2, C502.2, C503.2, C504.2, C505.2, R500.2, R501.2, R504.2; also elsewhere on the board
unnamed: Q500.3 (B), Q501.3 (B), U501.6 (OUT)
unnamed: R501.1, R502.2, U500.3 (IN+)
unnamed: C500.2, R500.1, U500.2 (IN-)
unnamed: R502.1, R503.2, TP500.1, U500.6 (OUT)
unnamed: R504.1, RV500.3, U501.3 (IN+)
unnamed: C503.1, R503.1, U501.2 (IN-)

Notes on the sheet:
Final Gain & Output Stage
Gain
DC Bias Removal & Initial Gain Stage
[${#}] ${TITLE}
DESIGN NOTE: The Pro-ject AC synchronous motor is 16V RMS, 2W. Current draw calculation: A = W/V = 2W / 16V = 0.125 A

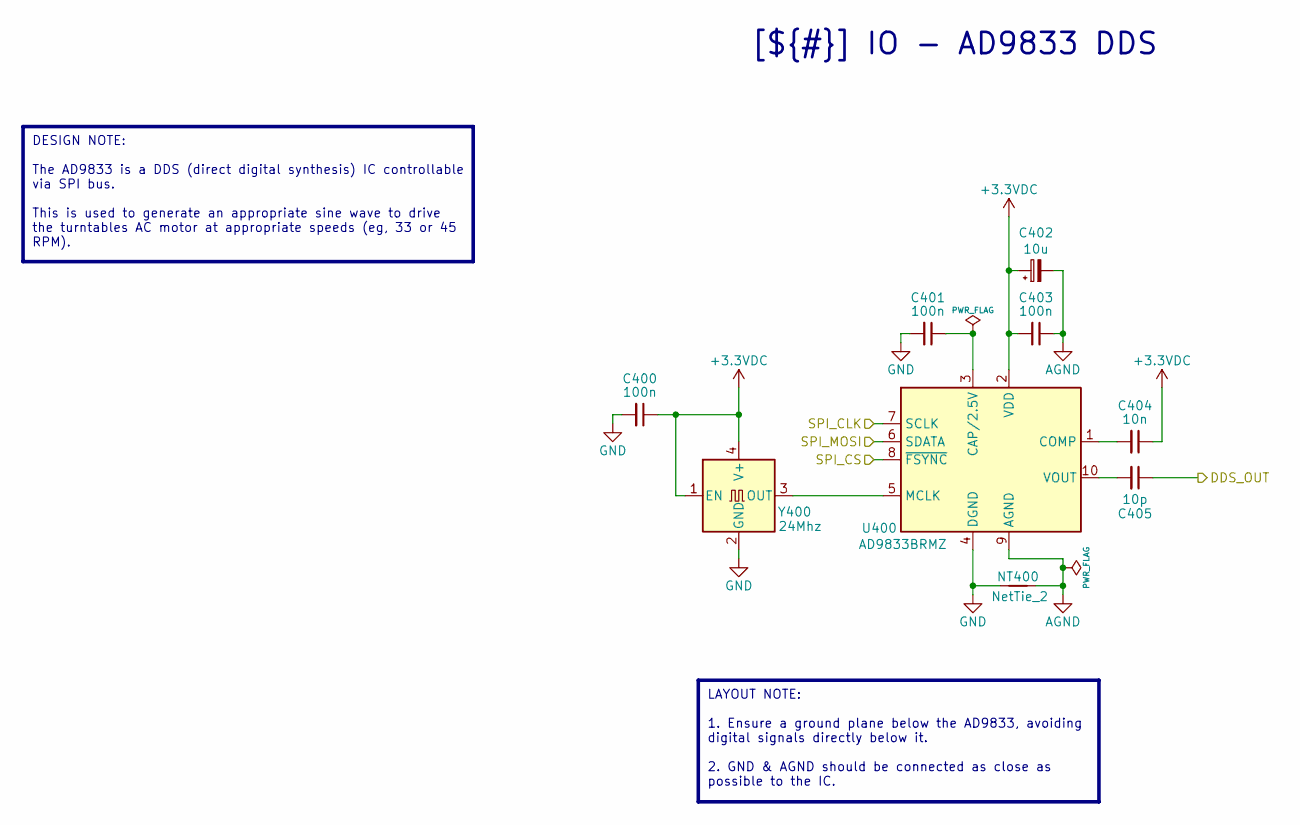
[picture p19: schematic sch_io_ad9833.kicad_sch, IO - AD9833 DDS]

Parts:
C400, C401, C403: 100n; C_0603_1608Metric; Digikey_PN 399-C0603C104K4RACTUCT-ND
C402: 10u; CP_EIA-3216-18_Kemet-A; Digikey_PN 399-8269-1-ND
C404: 10n; C_0603_1608Metric; Digikey_PN 311-3369-1-ND
C405: 10p; C_0603_1608Metric; Digikey_PN 732-7760-1-ND
NT400: NetTie_2; NetTie-2_SMD_Pad0.5mm
U400: AD9833BRMZ; MSOP-10_3x3mm_P0.5mm; Digikey_PN AD9833BRMZ
Y400: 24Mhz; Oscillator_SMD_EuroQuartz_XO32-4Pin_3.2x2.5mm; Digikey_PN 1908-O240-JO32-B-1V3-1-T1-LFCT-ND

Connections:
+3.3VDC: C400.1, C402.1, C403.2, C404.1, U400.2 (VDD), Y400.1 (EN), Y400.4 (V+); also elsewhere on the board
/IO - AD9833 DDS/DDS_OUT: C405.1; also elsewhere on the board
/IO - AD9833 DDS/SPI_CLK: U400.7 (SCLK); also elsewhere on the board
/IO - AD9833 DDS/SPI_CS: U400.8 (~FSYNC); also elsewhere on the board
/IO - AD9833 DDS/SPI_MOSI: U400.6 (SDATA); also elsewhere on the board
AGND: C402.2, C403.1, NT400.2, U400.9 (AGND)
GND: C400.2, C401.2, NT400.1, U400.4 (DGND), Y400.2 (GND); also elsewhere on the board
unnamed: C401.1, U400.3 (CAP/2.5V)
unnamed: C404.2, U400.1 (COMP)
unnamed: U400.5 (MCLK), Y400.3 (OUT)
unnamed: C405.2, U400.10 (VOUT)

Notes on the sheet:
[${#}] ${TITLE}
LAYOUT NOTE: 1. Ensure a ground plane below the AD9833, avoiding digital signals directly below it. 2. GND & AGND should be connected as close as possible to the IC.
DESIGN NOTE: The AD9833 is a DDS (direct digital synthesis) IC controllable via SPI bus. This is used to generate an appropriate sine wave to drive the turntables AC motor at appropriate speeds (eg, 33 or 45 RPM).

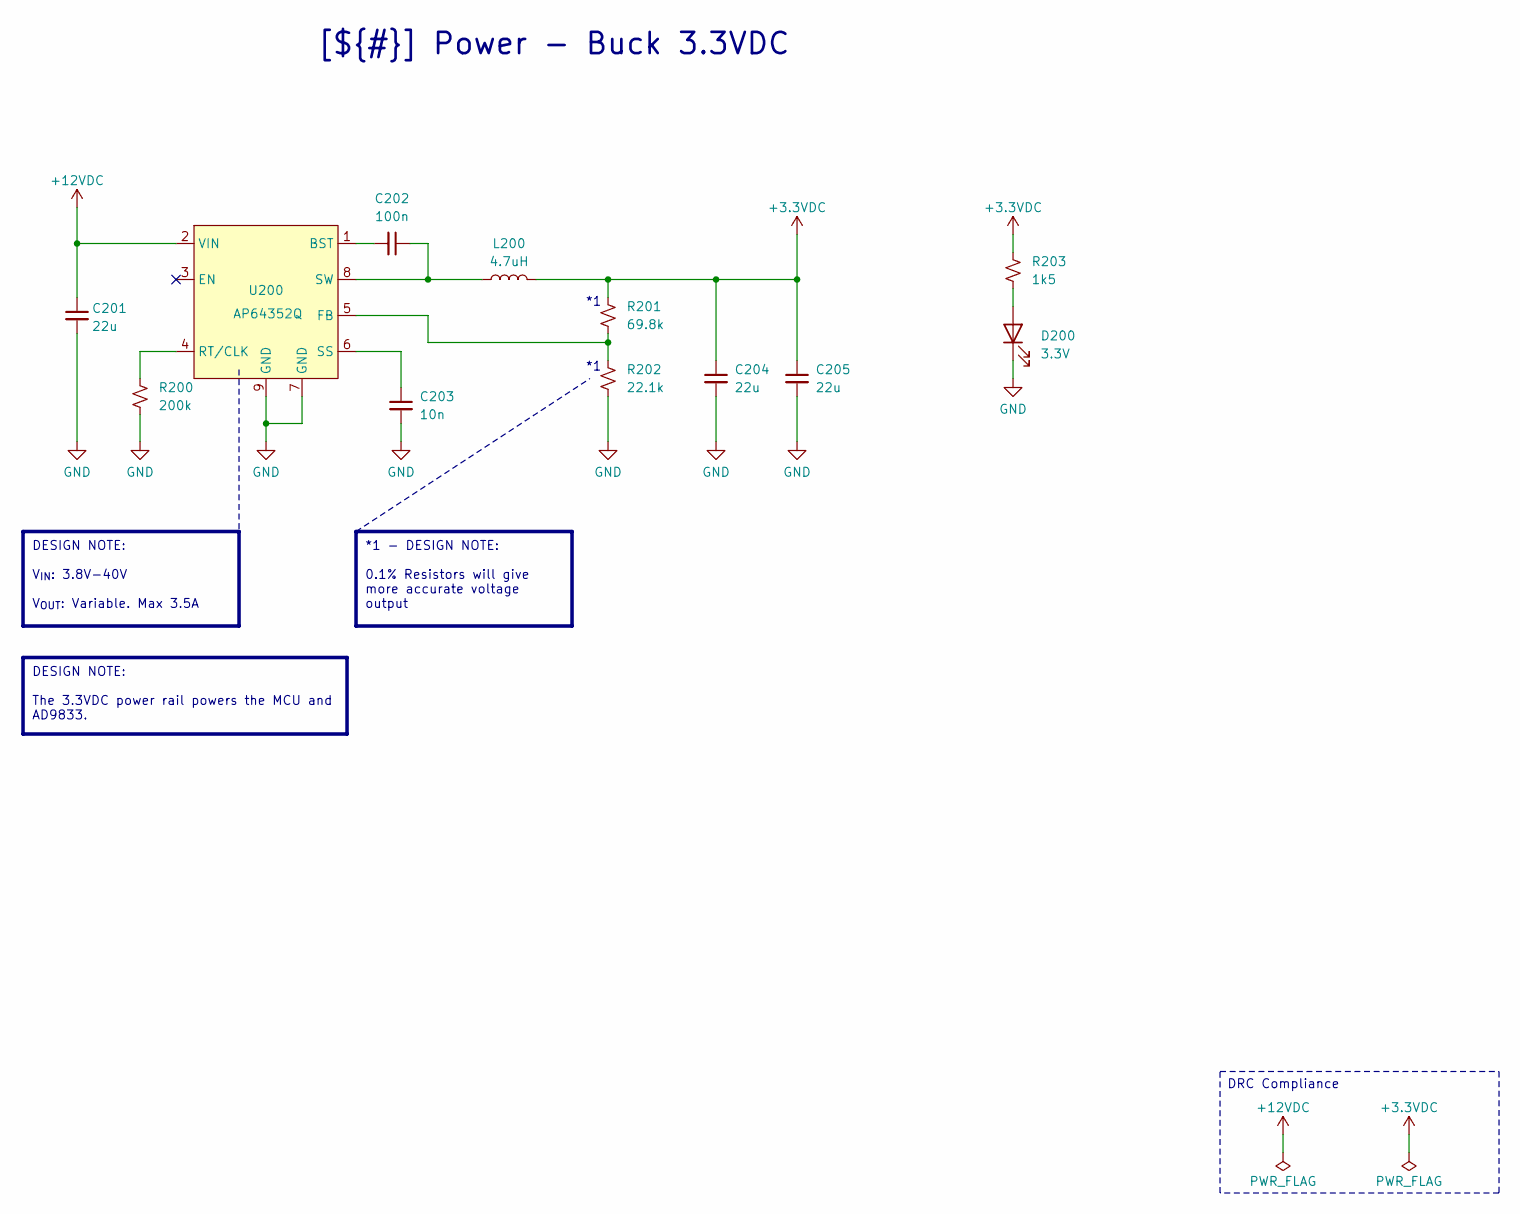
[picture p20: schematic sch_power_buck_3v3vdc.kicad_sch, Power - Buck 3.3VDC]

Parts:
C201, C204, C205: 22u; C_0805_2012Metric; Digikey_PN 445-14428-1-ND
C202: 100n; C_0603_1608Metric; Digikey_PN 399-C0603C104K4RACTUCT-ND
C203: 10n; C_0603_1608Metric; Digikey_PN 311-3369-1-ND
D200: 3.3V; LED_0603_1608Metric; Digikey_PN 732-4978-1-ND
L200: 4.7uH; Bournes_SRP4020TA-4R7M; Digikey_PN SRP4020TA-4R7MCT-ND
R200: 200k; R_0603_1608Metric; Digikey_PN MCT0603-200K-CFCT-ND
R201: 69.8k; R_0603_1608Metric; Digikey_PN 2019-RN73R1JTTD6982B25CT-ND
R202: 22.1k; R_0603_1608Metric; Digikey_PN YAG1590CT-ND
R203: 1k5; R_0603_1608Metric; Digikey_PN 311-1.5KGRCT-ND
U200: AP64352Q; AP64352QSP-13; Digikey_PN 31-AP64352QSP-13CT-ND

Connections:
+3.3VDC: C204.1, C205.1, L200.2, R201.1, R203.1; also elsewhere on the board
+12VDC: C201.1, U200.2 (VIN); also elsewhere on the board
GND: C201.2, C203.2, C204.2, C205.2, D200.1 (K), R200.2, R202.2, U200.7 (GND), U200.9 (GND); also elsewhere on the board
unnamed: D200.2 (A), R203.2
unnamed: C202.2, U200.1 (BST)
unnamed: R201.2, R202.1, U200.5 (FB)
unnamed: R200.1, U200.4 (RT/CLK)
unnamed: C203.1, U200.6 (SS)
unnamed: C202.1, L200.1, U200.8 (SW)

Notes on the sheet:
DRC Compliance
DESIGN NOTE: V_{IN}: 3.8V-40V V_{OUT}: Variable. Max 3.5A
[${#}] ${TITLE}
*1 - DESIGN NOTE: 0.1% Resistors will give more accurate voltage output
DESIGN NOTE: The 3.3VDC power rail powers the MCU and AD9833.

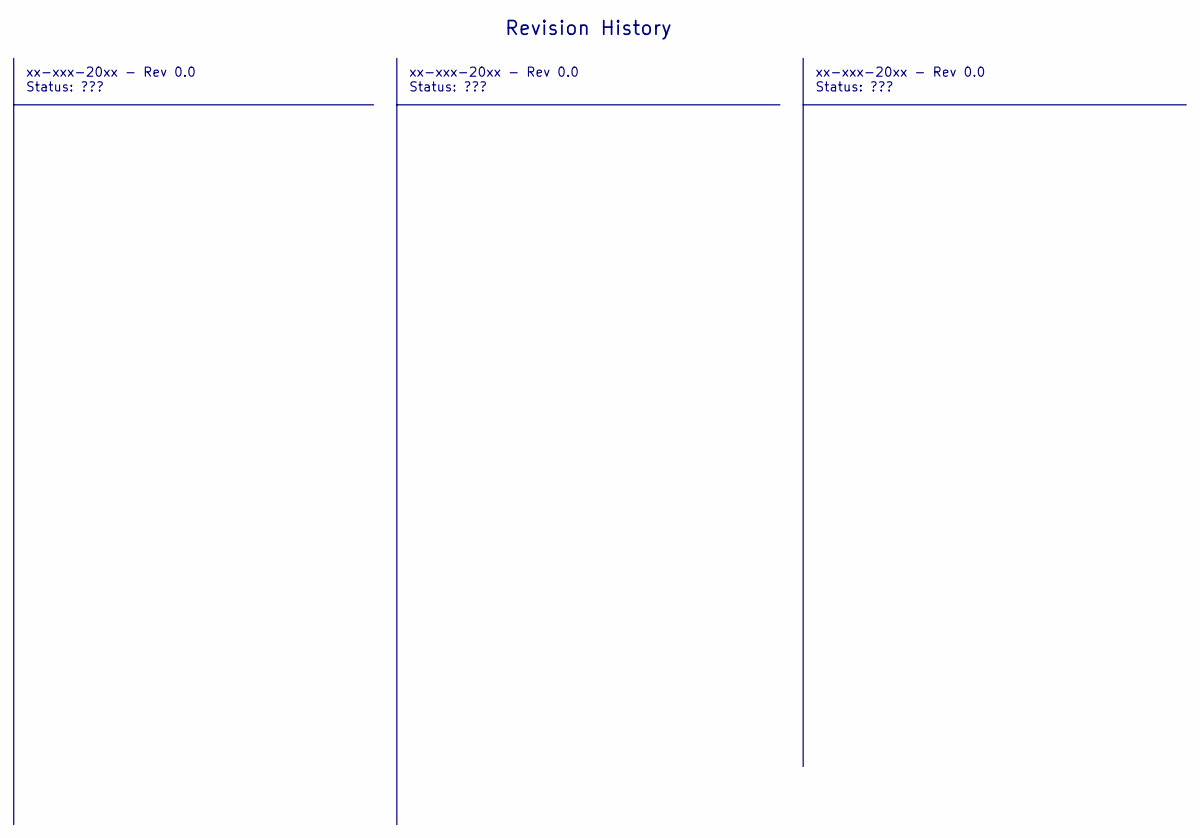
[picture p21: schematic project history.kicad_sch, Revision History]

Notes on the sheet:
xx-xxx-20xx - Rev 0.0 Status: ???
${TITLE}

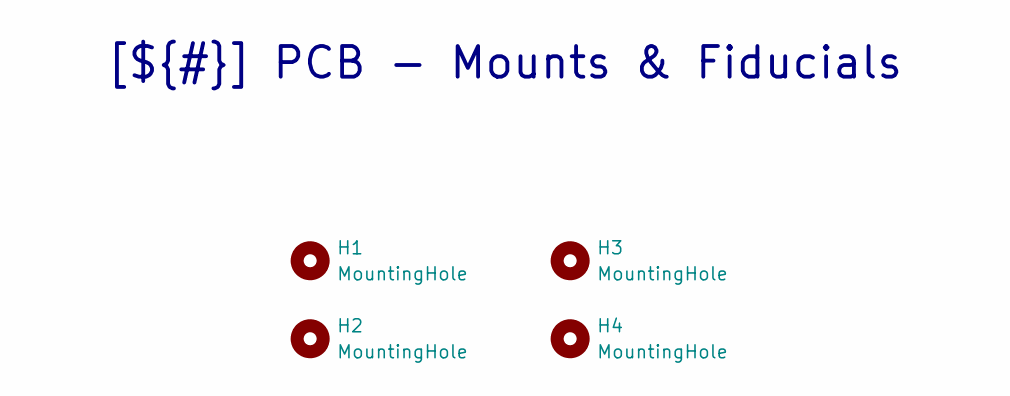
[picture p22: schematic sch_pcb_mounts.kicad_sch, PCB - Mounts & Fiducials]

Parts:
H1, H2, H3, H4: MountingHole; MountingHole_2.5mm

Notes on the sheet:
[${#}] ${TITLE}

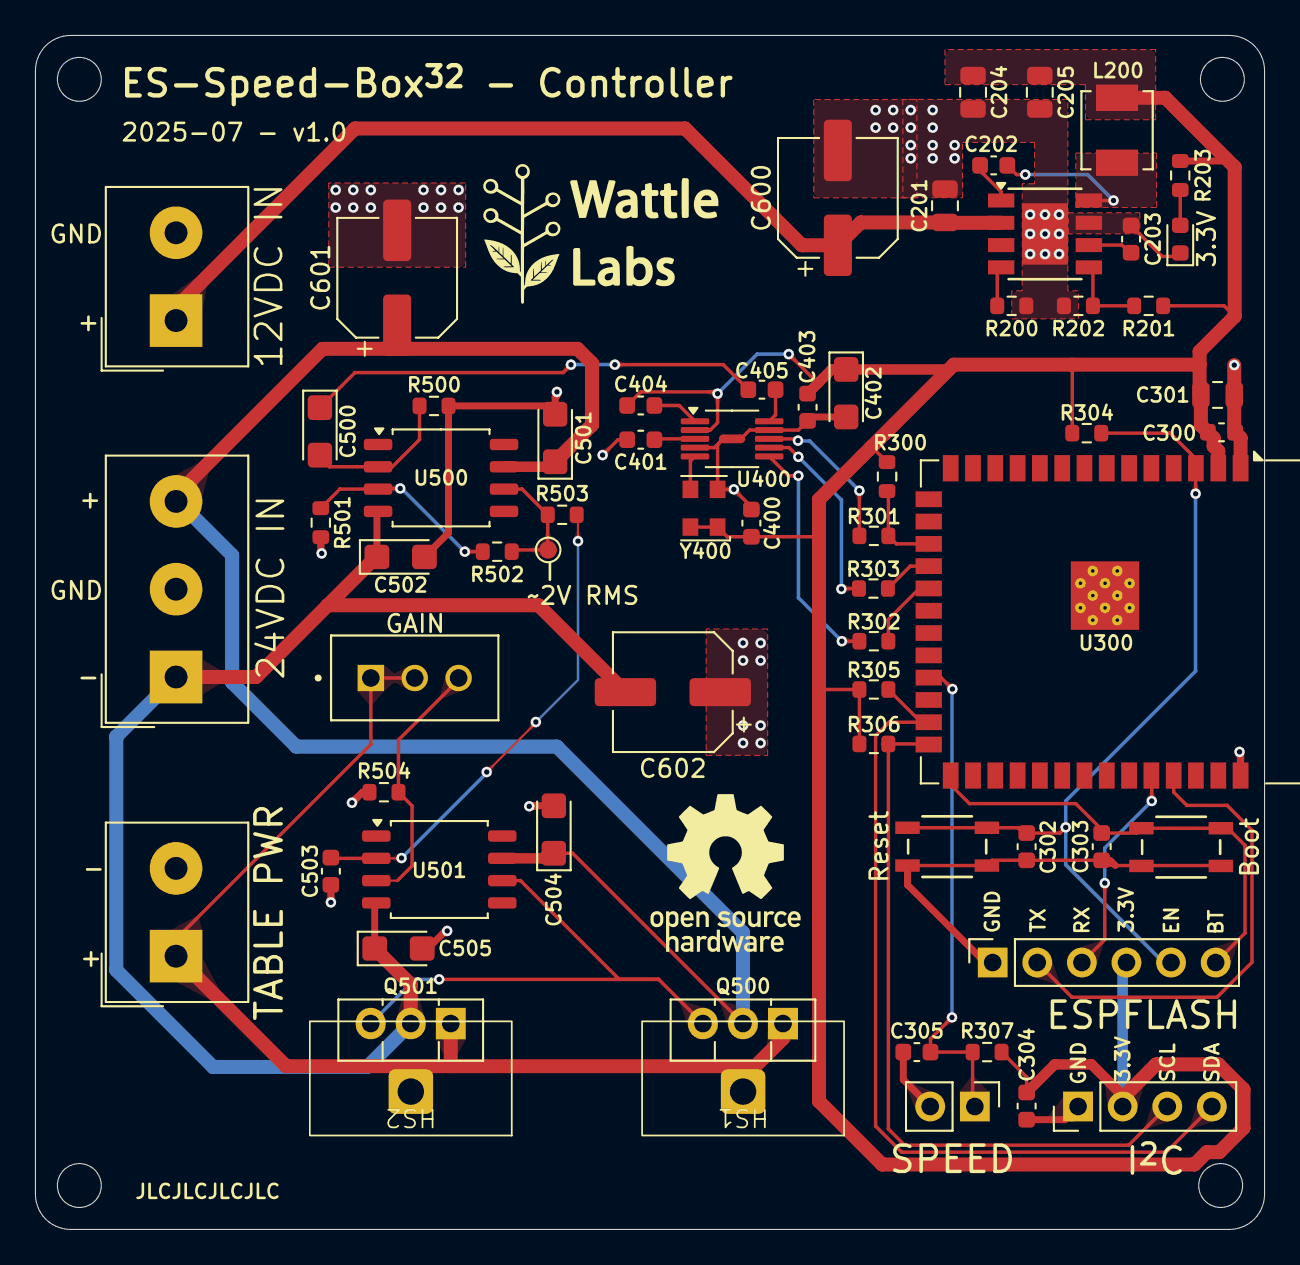
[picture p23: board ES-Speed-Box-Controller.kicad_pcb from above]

Board: 2 copper layers, 70.0 x 68.0 mm, 70 parts (0 on the bottom side), 37 nets.

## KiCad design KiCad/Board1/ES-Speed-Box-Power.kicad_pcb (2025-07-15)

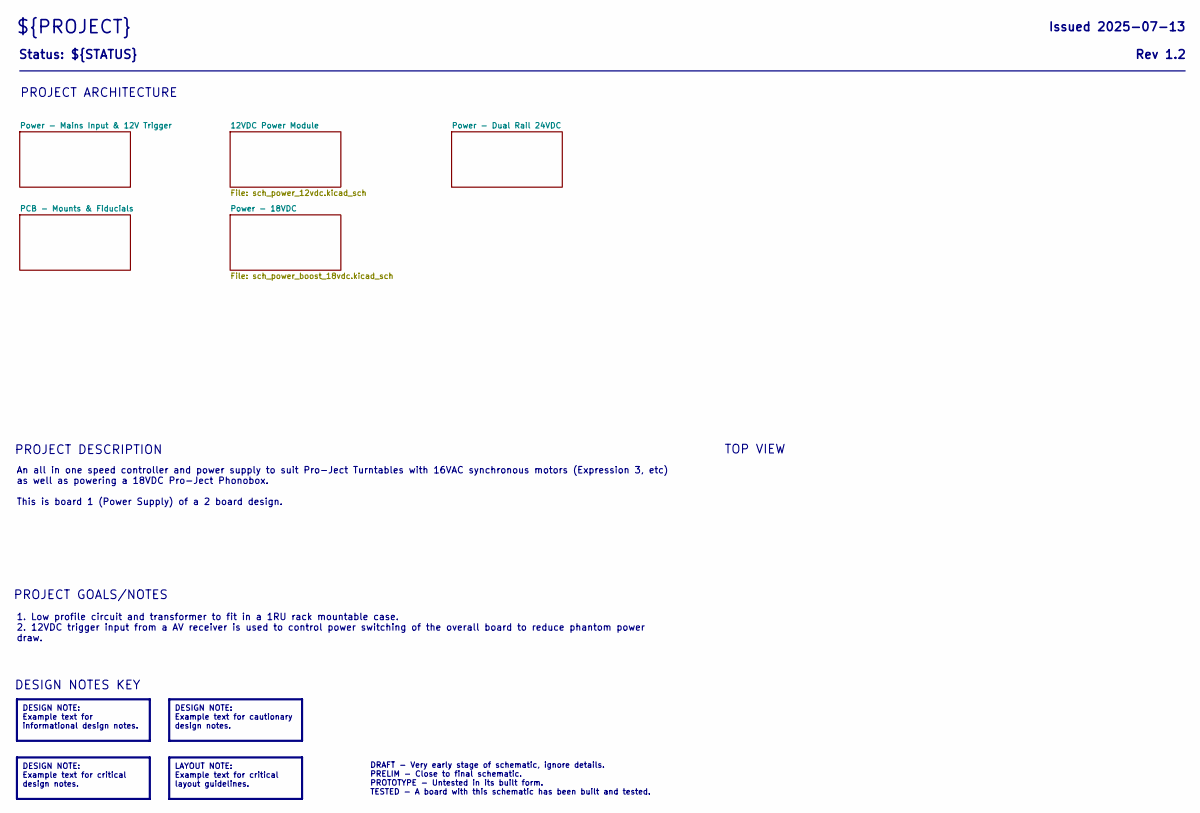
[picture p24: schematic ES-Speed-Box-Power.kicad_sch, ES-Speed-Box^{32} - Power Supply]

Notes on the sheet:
TOP VIEW
PROJECT DESCRIPTION
PROJECT GOALS/NOTES
PROJECT ARCHITECTURE
DESIGN NOTES KEY
${PROJECT}
Status: ${STATUS}
1. Low profile circuit and transformer to fit in a 1RU rack mountable case. 2. 12VDC trigger input from a AV receiver is used to control power switching of the overall board to reduce phantom power draw.
DESIGN NOTE: Example text for critical design notes.
DESIGN NOTE: Example text for cautionary design notes.
Issued ${ISSUE_DATE}
Rev ${REVISION}
LAYOUT NOTE: Example text for critical layout guidelines.
DRAFT - Very early stage of schematic, ignore details. PRELIM - Close to final schematic. PROTOTYPE - Untested in its built form. TESTED - A board with this schematic has been built and tested.
An all in one speed controller and power supply to suit Pro-Ject Turntables with 16VAC synchronous motors (Expression 3, etc) as well as powering a 18VDC Pro-Ject Phonobox. This is board 1 (Power Supply) of a 2 board design.
DESIGN NOTE: Example text for informational design notes.

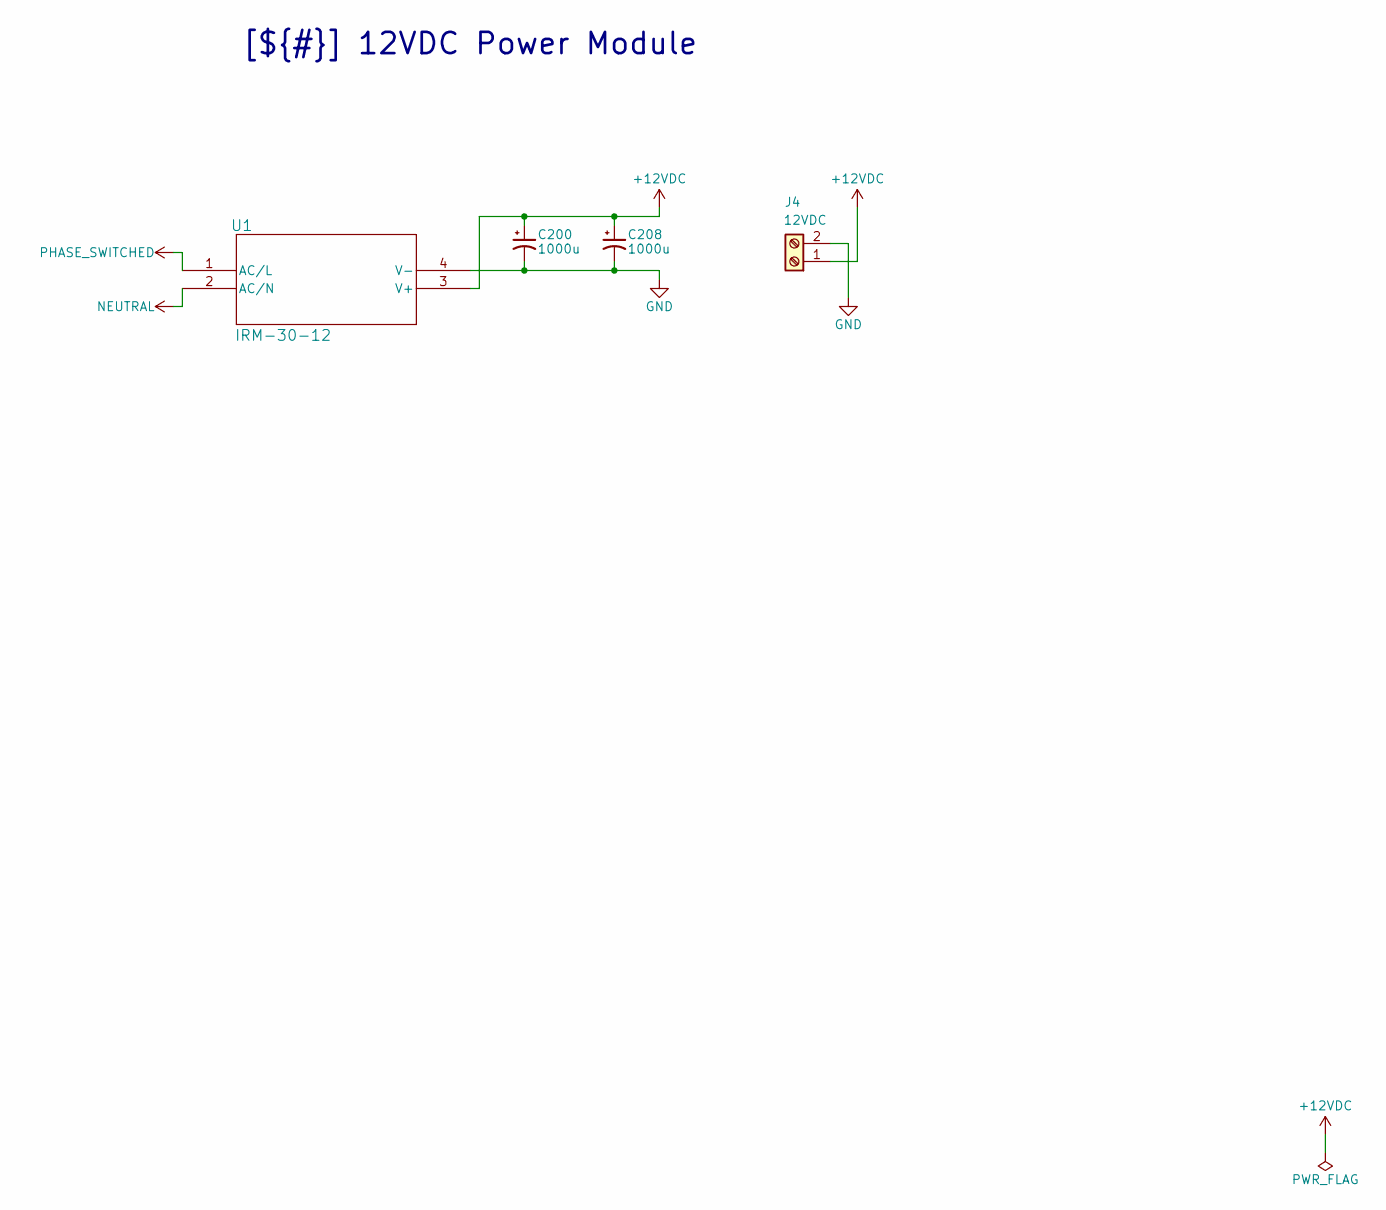
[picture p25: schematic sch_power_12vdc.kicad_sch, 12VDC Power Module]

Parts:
C200, C208: 1000u; CP_Radial_D13.0mm_P5.00mm
J4: 12VDC; TerminalBlock_1x02_P5.00mm
U1: IRM-30-12; Digikey_PN 1866-3043-ND

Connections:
+12VDC: C200.1, C208.1, J4.1, U1.3 (V+); also elsewhere on the board
GND: C200.2, C208.2, J4.2, U1.4 (V-); also elsewhere on the board
NEUTRAL: U1.2 (AC/N); also elsewhere on the board
PHASE_SWITCHED: U1.1 (AC/L); also elsewhere on the board

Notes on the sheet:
[${#}] ${TITLE}

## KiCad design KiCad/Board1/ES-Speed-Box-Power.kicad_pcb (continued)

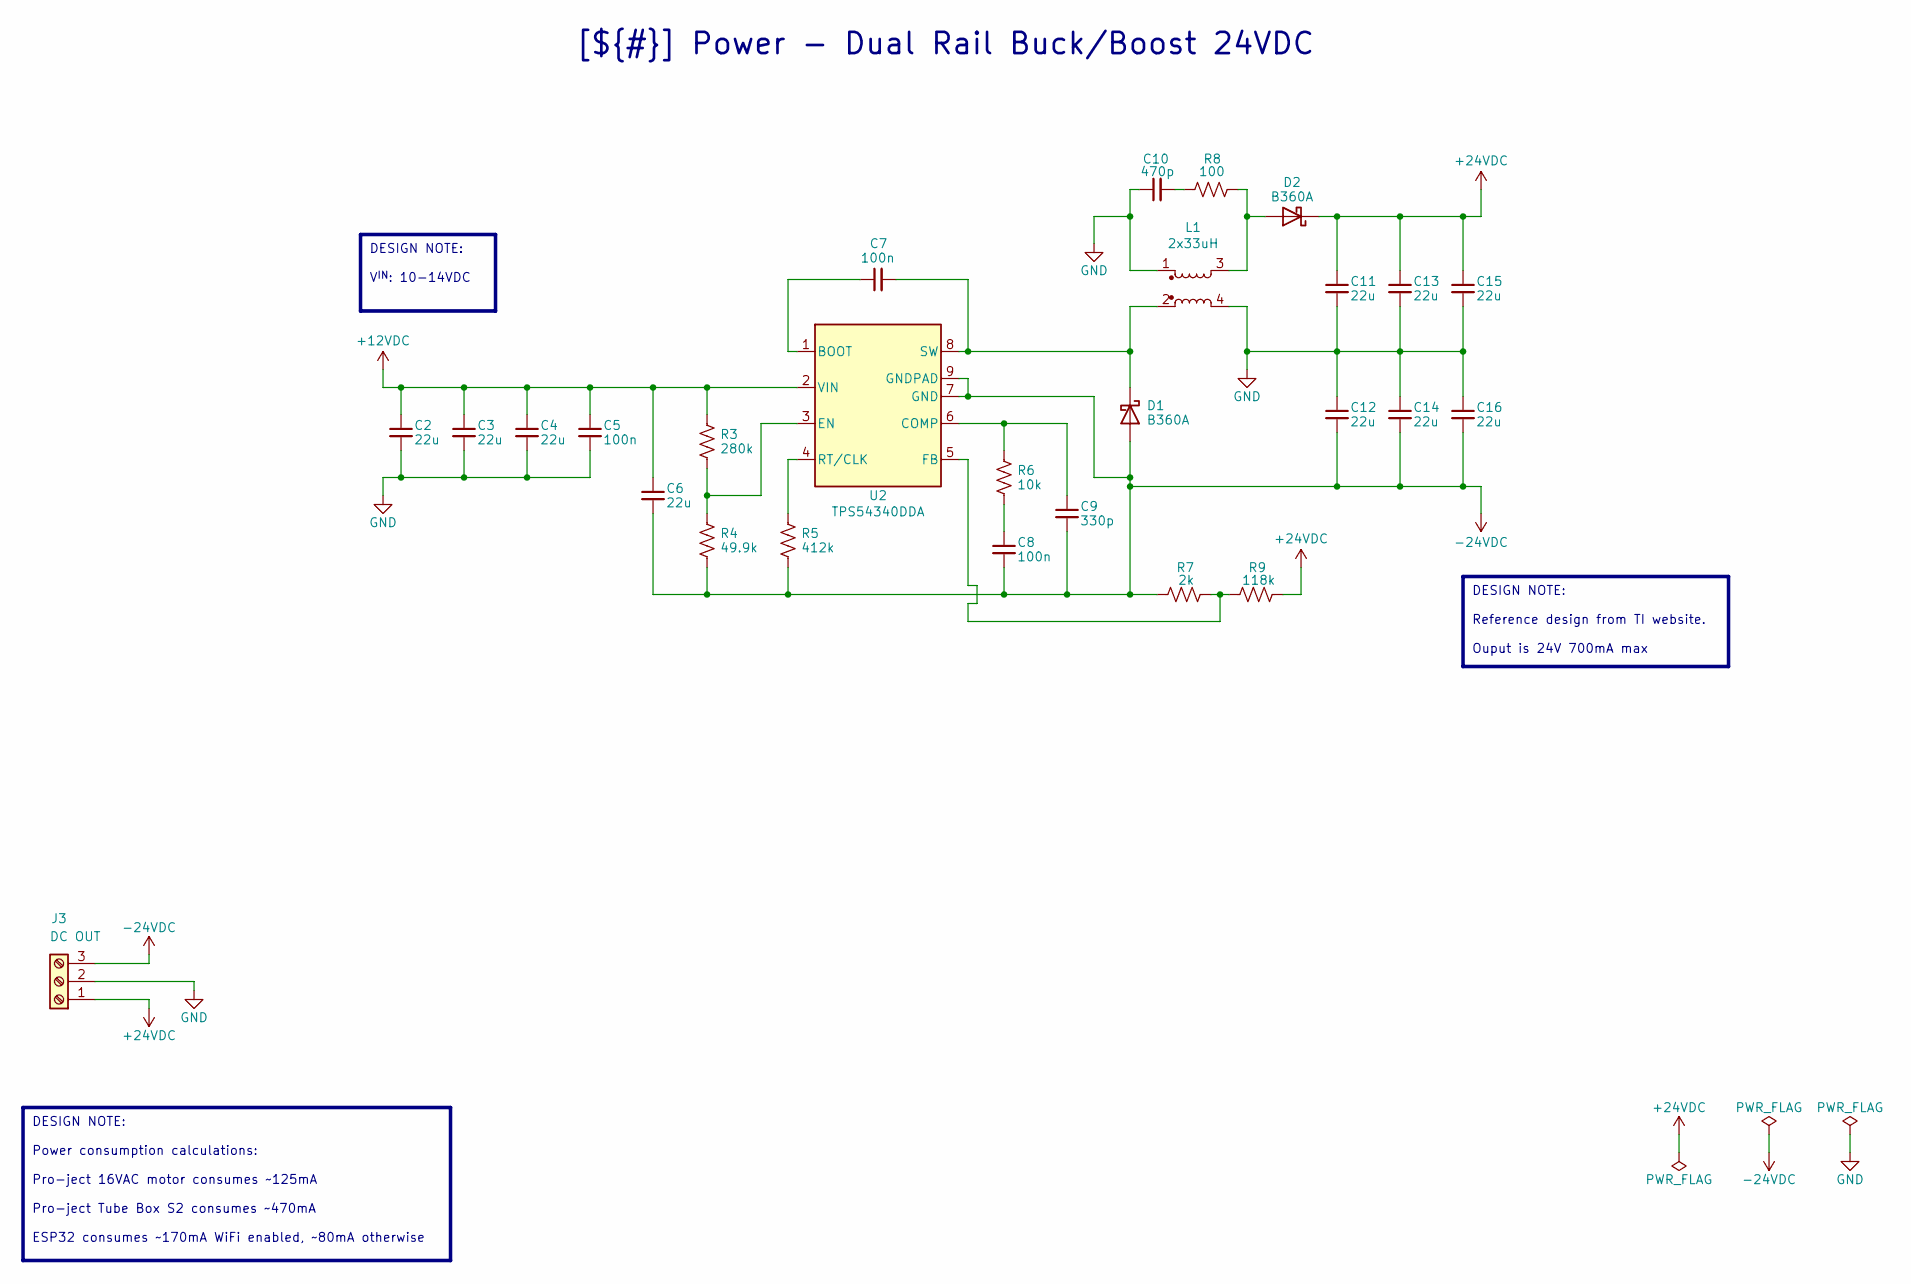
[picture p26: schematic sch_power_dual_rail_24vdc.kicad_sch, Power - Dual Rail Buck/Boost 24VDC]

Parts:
C2, C3, C4, C6, C11, C12, C13, C14, C15, C16: 22u; C_0805_2012Metric; Digikey_PN 445-14428-1-ND
C5, C7, C8: 100n; C_0603_1608Metric; Digikey_PN 587-3354-1-ND
C9: 330p; C_0603_1608Metric; Digikey_PN 399-C0603C331K5RACTUCT-ND
C10: 470p; C_0603_1608Metric; Digikey_PN 399-C0603C471F5GACTUCT-ND
D1, D2: B360A; D_SMA; Digikey_PN B360A-M3/61TGICT-ND
J3: DC OUT; TerminalBlock_1x03_P5.00mm
L1: 2x33uH; Bournes_SRF1260-330M; Digikey_PN SRF1260-330MCT-ND
R3: 280k; R_0603_1608Metric; Digikey_PN 311-280KHRCT-ND
R4: 49.9k; R_0603_1608Metric; Digikey_PN 541-3989-1-ND
R5: 412k; R_0603_1608Metric; Digikey_PN 311-412KHRCT-ND
R6: 10k; R_0603_1608Metric; Digikey_PN A121523CT-ND
R7: 2k; R_0603_1608Metric; Digikey_PN 541-3953-1-ND
R8: 100; R_0603_1608Metric; Digikey_PN 311-100HRCT-ND
R9: 118k; R_0603_1608Metric; Digikey_PN 541-118KHCT-ND
U2: TPS54340DDA; TI_SO-PowerPAD-8_ThermalVias; Digikey_PN 296-35495-5-ND

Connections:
+12VDC: C2.1, C3.1, C4.1, C5.1, C6.1, R3.1, U2.2 (VIN); also elsewhere on the board
+24VDC: C11.1, C13.1, C15.1, D2.1 (K), J3.1, R9.2
-24VDC: C6.2, C8.2, C9.2, C12.2, C14.2, C16.2, D1.2 (A), J3.3, R4.2, R5.2, R7.1, U2.7 (GND), U2.9 (GNDPAD)
GND: C2.2, C3.2, C4.2, C5.2, C10.1, C11.2, C12.1, C13.2, C14.1, C15.2, C16.1, J3.2, L1.1, L1.4; also elsewhere on the board
unnamed: C8.1, R6.2
unnamed: C10.2, R8.1
unnamed: C7.2, D1.1 (K), L1.2, U2.8 (SW)
unnamed: D2.2 (A), L1.3, R8.2
unnamed: C7.1, U2.1 (BOOT)
unnamed: C9.1, R6.1, U2.6 (COMP)
unnamed: R3.2, R4.1, U2.3 (EN)
unnamed: R7.2, R9.1, U2.5 (FB)
unnamed: R5.1, U2.4 (RT/CLK)

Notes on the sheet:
[${#}] ${TITLE}
DESIGN NOTE: Power consumption calculations: Pro-ject 16VAC motor consumes ~125mA Pro-ject Tube Box S2 consumes ~470mA ESP32 consumes ~170mA WiFi enabled, ~80mA otherwise
DESIGN NOTE: Reference design from TI website. Ouput is 24V 700mA max
DESIGN NOTE: V^{IN}: 10-14VDC


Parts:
C1: 10n; C_Rect_L18.0mm_W5.0mm_P15.00mm_FKS3_FKP3; Digikey_PN BFC233841103-ND
J1: 230VAC IN; TerminalBlock_1x05_P5.00mm
J2: 12V Trigger Input; TerminalBlock_1x02_P5.00mm
R1, R2: 2M; R_2010_5025Metric_Pad1.40x2.65mm_HandSolder; Digikey_PN 2019-HV732HTTE2004FCT-ND
RV1: 10D561; RV_Disc_D12mm_W6.1mm_P7.5mm; Digikey_PN 118-MOV-10D561K-ND
S1: AQG22212; Digikey_PN 255-3751-ND

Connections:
/Power - Mains Input & 12V Trigger/TRIGGER+: J2.1, S1.3 (IN+)
/Power - Mains Input & 12V Trigger/TRIGGER-: J2.2, S1.4 (IN-)
EARTH: J1.1
NEUTRAL: C1.2, J1.5, R2.2, RV1.2; also elsewhere on the board
unnamed: R1.2, R2.1
PHASE: C1.1, J1.3, R1.1, RV1.1, S1.1 (OUT1)
PHASE_SWITCHED: S1.2 (OUT2); also elsewhere on the board

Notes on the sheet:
DESIGN NOTE: Skipped pins 2&4 on J1/J2 is intended to provide additional trace clearance VS finding a larger part. Copper to be removed from unconnected PCB holes.
[${#}] ${TITLE}
DESIGN NOTE: 12V trigger comes from audio amplifier. The design goal here is to allow the audio amp to control when power is supplied to the overall circuit to reduce phantom power. In my use case, the audio amp can trigger its 12v outputs based on audio input. I.e., the circuit, turntable, and pho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
DESIGN NOTE: Mains side 2A fuse is intended to be offboard (being built into an IEC power receptable).


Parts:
C201, C202: 10u; C_0805_2012Metric; Digikey_PN 490-10515-1-ND
C203: 47n; C_0603_1608Metric; Digikey_PN 490-5854-1-ND
C204: 15n; C_0603_1608Metric; Digikey_PN 311-1430-1-ND
C205, C206, C207: 4.7; C_0805_2012Metric; Digikey_PN 490-10751-1-ND
D200: B360B-13-F; D_SMB; Digikey_PN B360B-FDICT-ND
J5: 18VDC; TerminalBlock_1x02_P5.00mm
L200: 10uH; Bournes_SRP5030T-100M; Digikey_PN SRP5030T-100MCT-ND
R200: 105k; R_0603_1608Metric; Digikey_PN 13-AC0603FR-07105KLCT-ND
R201: 3.83k; R_0603_1608Metric; Digikey_PN 311-3.83KHRCT-ND
R202: 221k; R_0603_1608Metric; Digikey_PN 311-221KHRCT-ND
R203: 16.2k; R_0603_1608Metric; Digikey_PN 311-16.2KHRCT-ND
U200: TPS61175PWPR; TPS61175; Digikey_PN 296-24013-1-ND

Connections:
+12VDC: C201.1, C202.1, L200.1, U200.3 (VIN), U200.4 (EN); also elsewhere on the board
+18VDC: C205.1, C206.1, C207.1, D200.1 (K), J5.1, R202.1
/Power - 18VDC/SW: D200.2 (A), L200.2, U200.1 (SW), U200.2 (SW__1)
GND: C201.2, C202.2, C203.2, C204.2, C205.2, C206.2, C207.2, J5.2, R200.2, R203.2, U200.6 (SYNC), U200.7 (AGND), U200.12 (PGND), U200.13 (PGND__1), U200.14 (PGND__2), U200.15 (EPAD); also elsewhere on the board
unnamed: C204.1, R201.2
unnamed: R201.1, U200.8 (COMP)
unnamed: R202.2, R203.1, U200.9 (FB)
unnamed: R200.1, U200.10 (FREQ)
unnamed: C203.1, U200.5 (SS)

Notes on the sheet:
DESIGN NOTE: The 18VDC power rail powers the external TubeBox II Phono Preamp.
[${#}] ${TITLE}


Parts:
H1, H2, H3, H4: MountingHole; MountingHole_2.2mm_M2

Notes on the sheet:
[${#}] ${TITLE}



Board: 2 copper layers, 100.0 x 94.0 mm, 57 parts (2 on the bottom side), 26 nets.

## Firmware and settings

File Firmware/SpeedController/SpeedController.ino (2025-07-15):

/* 
Proof of concept firmware to generate a SIN waveform and cycle between 50 and 67Hz every 10 seconds
*/

// WiFi credentials
#include <credentials.h>

#include <Arduino.h>
#include <WiFi.h>
#include <PrettyOTA.h>

#include <SPI.h>
#include <Wire.h>

#include <SimpleAD9833.h>

// Define the SPI pins for the AD9833 DDS
const uint8_t SCLK_PIN = 18;
const uint8_t DATA_PIN = 23;
const uint8_t CS_PIN = 5;

AsyncWebServer  server(80); // Server on port 80 (HTTP)
PrettyOTA OTAUpdates;

// Instantiate the SimpleAD9833 object with the chip select (CS) pin
SimpleAD9833 myWaveform(CS_PIN);

void setup() {
  Serial.begin(115200);
  Serial.println("Booting");

  pinMode(2, OUTPUT);

  // Initialise SPI communication using the defined pins
  SPI.begin(SCLK_PIN, -1, DATA_PIN);
  Serial.println("Starting SPI");


  // Initialize WiFi
  WiFi.begin(WIFI_SSID, WIFI_PASSWORD);

  // Wait for successful WiFi connection
  while (WiFi.waitForConnectResult() != WL_CONNECTED)
  {
      Serial.println("[WiFi] Connection failed! Rebooting...");
      delay(3000);
      ESP.restart();
  }

    // Print IP address
    Serial.println("PrettyOTA can be accessed at: http://" + WiFi.localIP().toString() + "/update");

    // Initialize PrettyOTA
    OTAUpdates.Begin(&server);

    // Set unique Hardware-ID for your hardware/board
    OTAUpdates.SetHardwareID("ES-SpeedBox-32");

    // Set firmware version to 1.0.0
    OTAUpdates.OverwriteAppVersion("0.0.1");

    // Set current build time and date
    PRETTY_OTA_SET_CURRENT_BUILD_TIME_AND_DATE();

    // Start web server
    server.begin();

  myWaveform.begin();
}

void loop() {
  myWaveform.setWaveform(SINE, 50);
  delay(20000);
  myWaveform.setWaveform(SINE, 67);
  delay(20000);
}

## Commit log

2025-07-15 Update gitignore
    [ES-Speed-Box-Controller.kicad_pcb, ES-Speed-Box-Controller.kicad_sch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]
2025-07-27 Tweaks to PCB
    DRC check exceptions. Produced gerbers for JLCPCB.
    [ES-Speed-Box-Controller-CuBottom.gbr, ES-Speed-Box-Controller-CuTop.gbr, ES-Speed-Box-Controller-EdgeCuts.gbr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]
